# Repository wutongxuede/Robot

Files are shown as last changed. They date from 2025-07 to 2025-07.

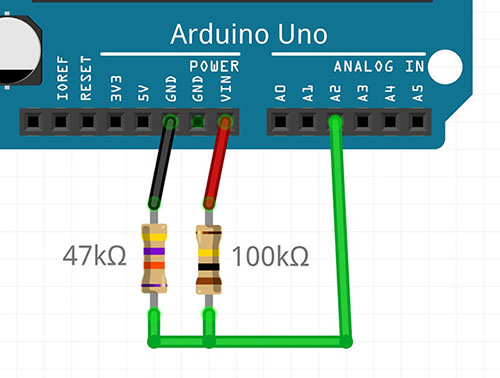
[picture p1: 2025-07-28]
Connection tutorial diagram/7.png

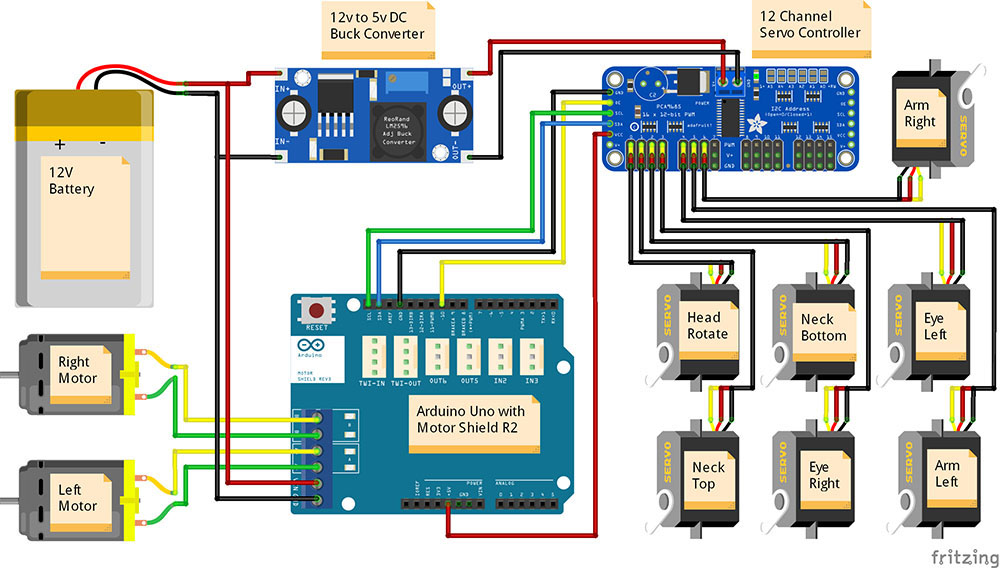
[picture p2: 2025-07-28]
Connection tutorial diagram/1.png

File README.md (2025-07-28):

# Robot
#Focus on discussions and sharing about Robot-Wall making or other DIY projects.

#The source code of the software is from the content published by Simon Bluett chillibasket on GitHub (Click to jump to GitHub for viewing: https://github.com/chillibasket/walle-replica)
## Basic introduction of the Wall-E model
1. Each eye can be independently controlled to rise and fall by a servo.

2. Each eye has space for a small camera. (We haven't done this part yet, so if you are interested, you can try it first)

3. The head can be turned left and right using a servo. (Due to the heavy weight of the head, it is recommended to use a hollow printing for the head)

4. Both joints of the neck are driven by servos, which allows the head to look up/down and raise/lower.

5. Each arm has a servo at the shoulder to move the arm up and down.

6. The arms are composed of pressure-fit joints, hands and fingers, and can be posed manually.

7. The tracks are fully 3D printed and can be driven using two 12V DC reduction motors.
**Flashing the program**
1. Please write the program to the Raspberry Pi and Arduino first, test it, and then install the circuit board into the robot.
2. The programming of the robot can be divided into two main parts; the Arduino code, and the web server on the Raspberry Pi.
Download/clone the folder wall-e from the online repository. (To add a voice recognition module, use our modified wall-e.ino main program, in the walle-replica-3.0 - modified version program folder)
Open wall-e.ino in the Arduino IDE;. In addition, the MotorController.hpp and Queue.hpp files will also automatically open on different tabs in the IDE.
Install the Adafruit_PWMServoDriver.h library
Go to Sketch -> Include Library -> Manage Libraries
Search for Adafruit PWM Servo Driver.
Install the latest version of the library
Connect the computer and the controller with a USB data cable. Make sure to select the correct board and port in the "Tools" menu.
Upload the wall-e.ino main program
**Test**
Upload the main program to the Arduino. While the Arduino is still connected to the computer, connect a 12V (3S) battery and power it on.
Open the serial port detection (the button on the upper right of the Arduino IDE), set the baud rate to 115200.
Now test the movement of Wally, send characters "w", "a", "s" or "d", which respectively represent Wally moving forward, left, backward or right. Sending 'q' can stop the movement.
Now test the head movement of Wally, send letters "j", "l", "i" or "k" to tilt the head left or right, and raise or lower the eyes. At this stage, the joints controlled by the servo motors may have a wider range than the actual due to the lack of setting for the stroke. This problem will be solved by performing the following servo calibration steps.
Servo Calibration
Download/clone the "wall-e_calibration" folder from the online repository.
Open wall-e_calibration.ino in the Arduino IDE.
Upload the program to the Arduino, open the serial monitor, and set the baud rate to 115200.
This program is used to calibrate the movement range required to move each servo motor to the corresponding position, the maximum and minimum PWM pulse widths. The standard LOW and HIGH positions of each servo are as follows.
Before installing the servo motors, it is necessary to ensure that the angles of the servo motors are correct (the range can be referred to the following figure), and then install the servo arms. Since the servo motors can only rotate 180 degrees, if they are fixed at the wrong angle, they will not be able to control the joints correctly.

After starting the program, open the serial monitor. After 2-3 seconds, a message should appear indicating that the LOW position of the first servo motor (head rotation) is ready for calibration.
Send the characters "a" and "d" to control the robot's movement forward and backward, within the range of -10 to +10. If more precise control is needed, use the characters "z" and "c" to move the robot, within the range of -1 to +1.
Once the servo is positioned at the correct position (as shown in the figure below), send the character "n" to continue the calibration steps. It will move to the HIGH position of the same servo, and then the 7 servos in the robot will repeat this process.
When all the joints have been calibrated, the program will output an array containing the calibration values to the serial monitor.
Copy this array and paste it into lines 144 to 150 of the wall-e - ino program. The array should look similar to the following:

int preset[][2] =  {{410,120},  // head rotation
                    {532,178},  // neck top
                    {120,310},  // neck bottom
                    {465,271},  // eye right
                    {278,479},  // eye left
                    {340,135},  // arm left
                    {150,360}}; // arm right
                    
**Battery level detection (optional)**
Note: When using batteries to power the robot, it is necessary to detect the battery level in real time. Over-discharge may cause battery damage, and insufficient power supply may damage the SD card of the Raspberry Pi. 
When using the battery level detection function on the Arduino, please connect the following resistors as shown in the following diagram and make the connections.

The resistor (voltage divider) reduces the 12V voltage to below 5V, allowing the Arduino to measure the voltage using its analog pins. The recommended resistor values are R1 = 100kΩ and R2 = 47kΩ.
In Arduino, remove line 54 of the main program wall-e.ino.
If you use different resistor values, please change the value of the voltage divider gain factor in line 54 of the program according to the formula: POT_DIV = R2 / (R1 + R2).
The program should now automatically check the battery level every 10 seconds, and this level will be displayed in the "Status" section of the Raspberry Pi network interface.
OLED display (optional) (Contributed by hpkevertje on GitHub) Notes for Attention

A 1.3-inch small OLED display can be integrated, and the battery level of the Wally robot can be displayed on the battery indicator panel. This function requires enabling the aforementioned battery detection circuit. The screen will be updated each time the battery level is calculated. 
This function uses the u8g2 display library in the page mode. 
On the Arduino UNO, you might receive a warning about high memory usage, but this warning can be ignored. 
To use the oLed display function on Arduino, connect the i2c oLed display (as shown in the picture) to the i2c bus of the servo motor module. 
Input image description 
Install the U8g2 library in the Arduino Library Manager:
In Sketch -> Include Library -> Manage Libraries
Search for U8gt (creator: oliver)
Install the latest version of the library
Define the OLED in the Arduino main program wall-e.ino.
If you are using another display method supported by the library, you can change the constructor on line 78 according to the documentation on the library reference page. The default is for the sh1106_128x64_name display.
Add custom servo actions (optional)
The source code comes with two animations that can be copied to replicate the scenes in the movie; 
The eye movements of robot Wally when it is activated, as well as a series of actions when robot Wally curiously looks around.

Starting from version 2.7, users can now add custom actions more easily. 
Open the "animations.ino" file, which is located in the same folder as the main Arduino program.
Each action command contains the position you want all the servos to move to, as well as the time the animation should wait before moving to the next instruction.
Actions can be added by inserting an additional case in the switch statement. Place the additional code above the default section in the empty space. For example: case 3:
// --- Title of your new motion sequence ---
//          time,head,necT,necB,eyeR,eyeL,armL,armR
queue.push({  12,  48,  40,   0,  35,  45,  60,  59});
queue.push({1500,  48,  40,  20, 100,   0,  80,  80});
// Add as many additional movements here as you need to complete the animation
// queue.push({time, head rotation, neck top, neck bottom, eye right, eye left, arm left, arm right})
break;
The time should be measured in milliseconds (for example, 3.5 seconds = 3500).
The position command for the servo needs to be an integer between 0 and 100, where 0 = LOW, 100 = HIGH, and the servo position calibrated in wall-e_calibration is the same.
If you want to disable a specific servo, you can set its value to -1.
Raspberry Pi Settings
Hardware Settings
Connect the power cable of the Raspberry Pi to the USB power output port of the 12V to 5V converter.
Connect the Arduino to the Raspberry Pi using a USB connection.
If you have a Raspberry Pi camera, connect the cable to the CSI camera connector.
For convenience in setting up and installing, you can insert the display into the HDMI port and connect a USB keyboard and mouse. Or connect and configure the Raspberry Pi from another computer via SSH.
Basic Settings
Install the Raspberry Pi to run the latest version of the Raspberry Pi OS Desktop. Installation instructions can be found on the Raspberry Pi website.
Ensure the Raspberry Pi is connected to the internet.
Open "Terminal" on the Raspberry Pi.
Clone the repository to the root directory of the Raspberry Pi:
cd ~

git clone https://github.com/chillibasket/walle-replica.git

The web interface settings can be configured by editing the "config.py" file:
Open the configuration file: nano ~/wall-replica/web_interface/config.py
On line 14, you can change the password for the web interface. The default password is "walle".
On line 15, you can set the default serial port for connecting to the Arduino. You can use the command "dmseg | grep tty" to find a list of all connected serial ports.
On lines 16 and 17, you can configure whether the Arduino and camera should automatically connect when starting the web server.
After completing the editing of the configuration, run the installation script and set all necessary libraries (it may take some time): cd ~/walle-replica

sudo chmod +x ./raspi-setup.sh

sudo ./raspi-setup.sh
Using the Web Server
If the installation is successful, when the Raspberry Pi is powered on, the web server will automatically start. This is accomplished using the Systemd service.
On the Raspberry Pi, you can view the web interface at http://localhost:5000
To view the interface from another computer on the same WiFi network, first you need to use the command hostname -I to determine the current IP address of the Raspberry Pi on the network
To access the web interface, open a browser on any computer/device in the same network and enter the IP address of the Raspberry Pi, followed by :5000. For example, 192.168.1.10:5000
To start controlling the robot, first ensure that the serial communication with Arduino has been initiated. To do this, go to the Settings tab in the web interface, select the correct serial port from the drop-down list, and then press the Reconnect button. If the configuration settings are correct, the device will automatically start.
Here are some commands for controlling the web interface: 
Stop the automatic web interface service: sudo systemd stop wall.service 
Disable startup on boot: sudo systemctl disable wall.service 
Re-enable the startup at boot time: sudo systemd enable wall.service 
Use the Blocky control (contributed by dkrey on GitHub) 
Starting from version 3.0, there is a new option in the web interface that allows robots to be controlled using graphical programming with drag-and-drop scripting languages. Just drag the operations you want to execute from the left sidebar and drop them into the editor area. For example, you can control Wally, rotate the motor, and play audio.
For commands to drive the motor, you may need to adjust the parameters from lines 25 to 28 at the bottom of the "config.py" file to ensure the correct speed and turning amount.
Using Blocky control (contributed by: dkrey on GitHub)
Starting from version 3.0, a new option has been added to the web interface, allowing robots to be controlled through graphical programming with drag-and-drop scripting languages. Just drag the operations you want to execute from the left sidebar and drop them into the editor area. For example, you can control Wally, rotate the motor, and play audio.
For commands to drive the motor, you may need to adjust the parameters from lines 25 to 28 at the bottom of the "config.py" file to ensure the correct speed and turning amount.
Adding video stream (optional)
The web server automatically supports any CSI connector connected to the Raspberry Pi and a ribbon cable camera. (Currently, USB network cameras are not supported.) 
Add new sound (optional)
By default, the Raspberry should automatically choose whether to output audio to the HDMI port or the headphone jack. However, the following command can be used to ensure that it always uses the headphone jack: amixer cset numid= 31
Make sure that all the sound files you want to use are of the *.wav format. Most music editors should be able to convert sound files to this format.
Modify the file name to have the format [group name][file name][sound duration (milliseconds)]. For example: voice_eva_1200.wav. In the web interface, audio files will be grouped by "group name" and sorted alphabetically.
Upload the sound files to the following folder on the Raspberry Pi: ~/wall -replica/web_interface/static/sounds/
When reloading the page, all the files should appear in the web interface. If the files do not appear, it may be necessary to change the permissions required to access this folder: sudo chmod -R 755 ~/wall -replica/web_interface/static/sounds

Set Raspberry Pi as a WiFi hotspot (optional)
The Raspberry Pi can be configured as a WiFi hotspot network. The computer/mobile phone/tablet controlling the robot can directly connect to this network.
To set up the WiFi hotspot, we will use the RaspAP project, which is responsible for all the configurations and tools to make the system work.
The following operations are based on the quick installation guide:
Update Raspian, kernel and firmware (and then restart): sudo apt-get update

sudo apt-get dist-upgrade

sudo reboot now

Make sure to set the correct WiFi country in the localization options of raspi-config: sudo raspi-config
Run the quick installation program: curl -sL https://install.raspap.com | bash
For the first few yes/no prompts during the installation process, enter "y" (yes) to accept all recommended settings.
The last two prompts (advertising interception and next) are not necessary, so you can enter "n" (no).
Restart the Raspberry Pi: sudo Reboot
Now the Raspberry Pi should start the WiFi hotspot network in the following way:
SSID (wifi name): raspi-webgui
Password: ChangeMe
After connecting to the WiFi network via a computer, mobile phone or tablet, enter the following address in the browser to open the Wally's network interface: http://10.3.141.1:5000
It is recommended to enter the WiFi configuration page at http://10.3.141.1 to modify the WiFi name and password. The default username is "admin" and the password is "secret".
Click on the "Hotspot" item in the left column. In the "Basic" tab, you can change the WiFi network name, and in the "Security" tab, you can change the WiFi password.
To change the admin password of the WiFi settings management interface, click the "admin" icon in the upper right corner of the interface.

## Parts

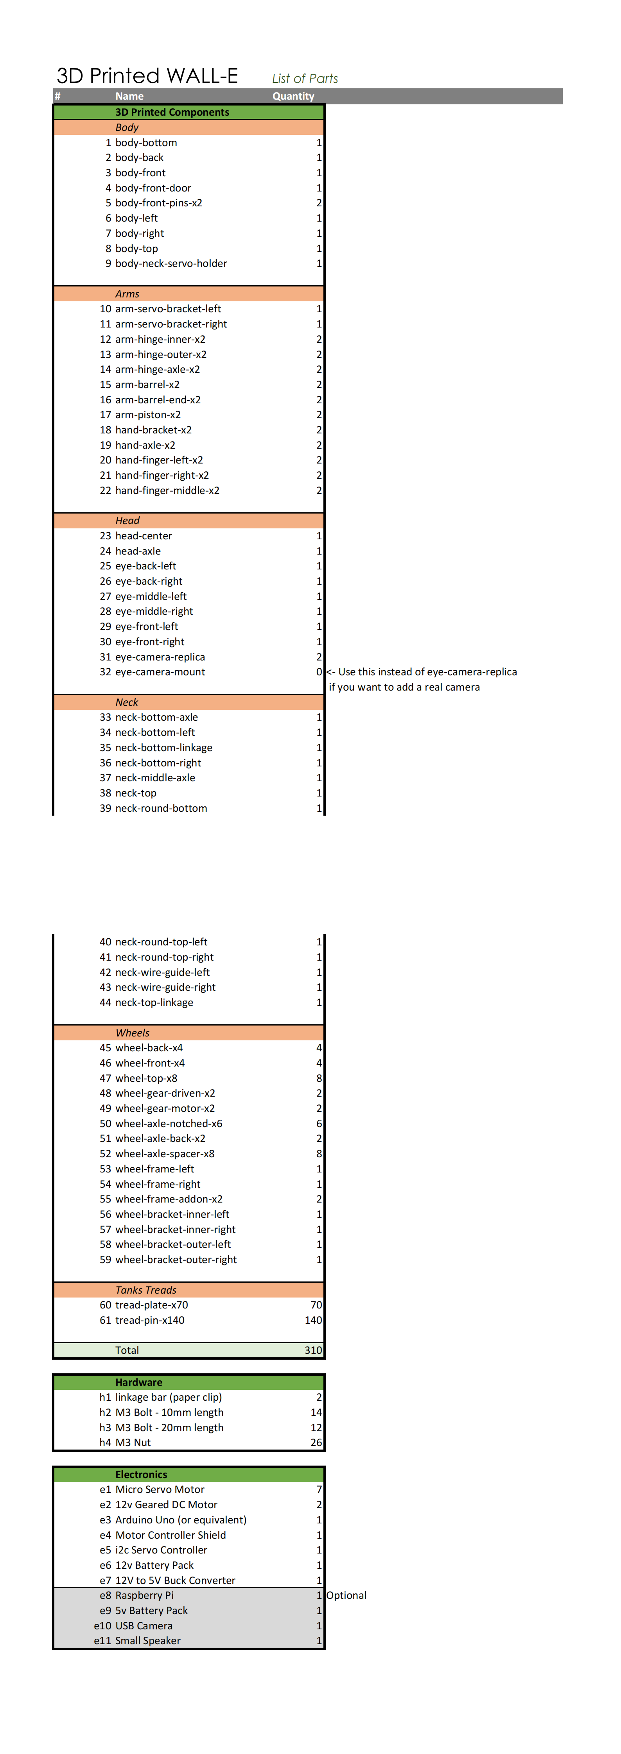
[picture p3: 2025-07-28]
Material purchase screenshot/Wall-Part quantity.png

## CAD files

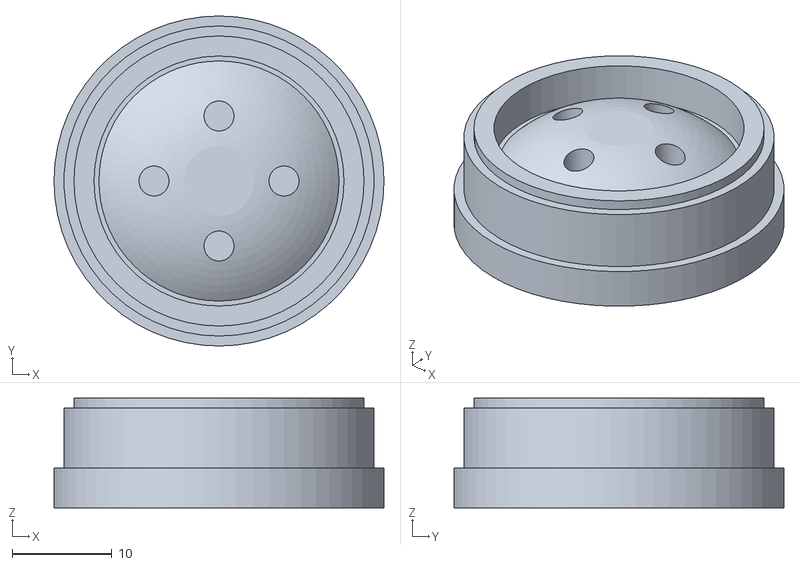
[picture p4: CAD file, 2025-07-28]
Robot-Wall 3D Printing Drawings/wheel-top-larger-x0.STL
33.0 x 33.0 x 11.0

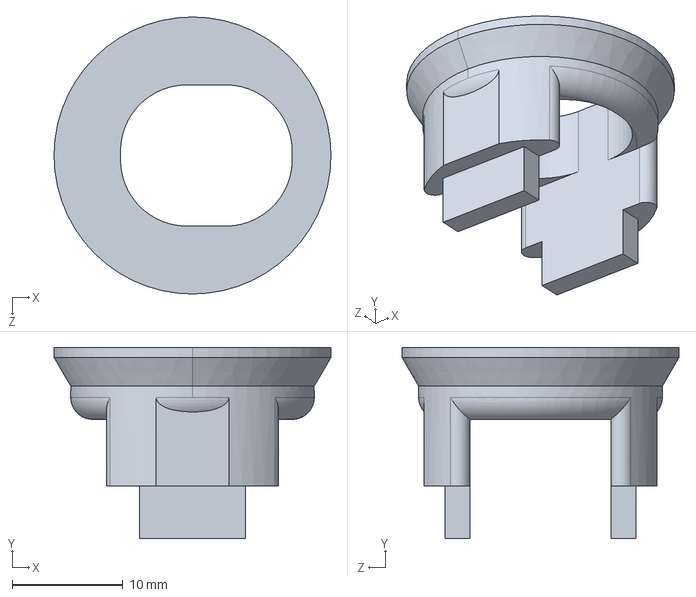
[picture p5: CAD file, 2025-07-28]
Robot-Wall drawing in STEP format, which can be used for modification/neck-round-bottom.STEP
25.0 x 17.2 x 25.0 mm

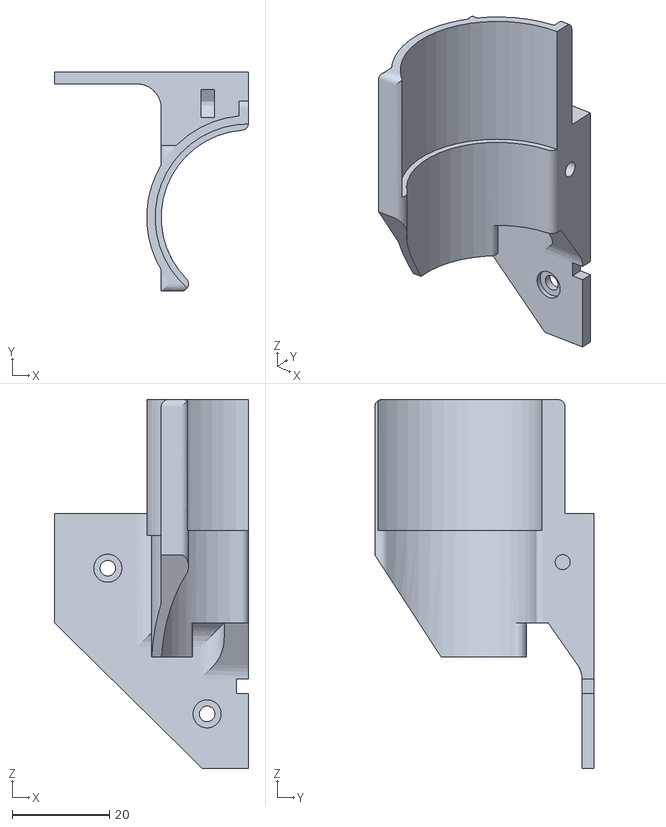
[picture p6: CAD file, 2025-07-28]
Robot-Wall 3D Printing Drawings/wheel-bracket-inner-right-3.STL
40.0 x 45.2 x 76.0

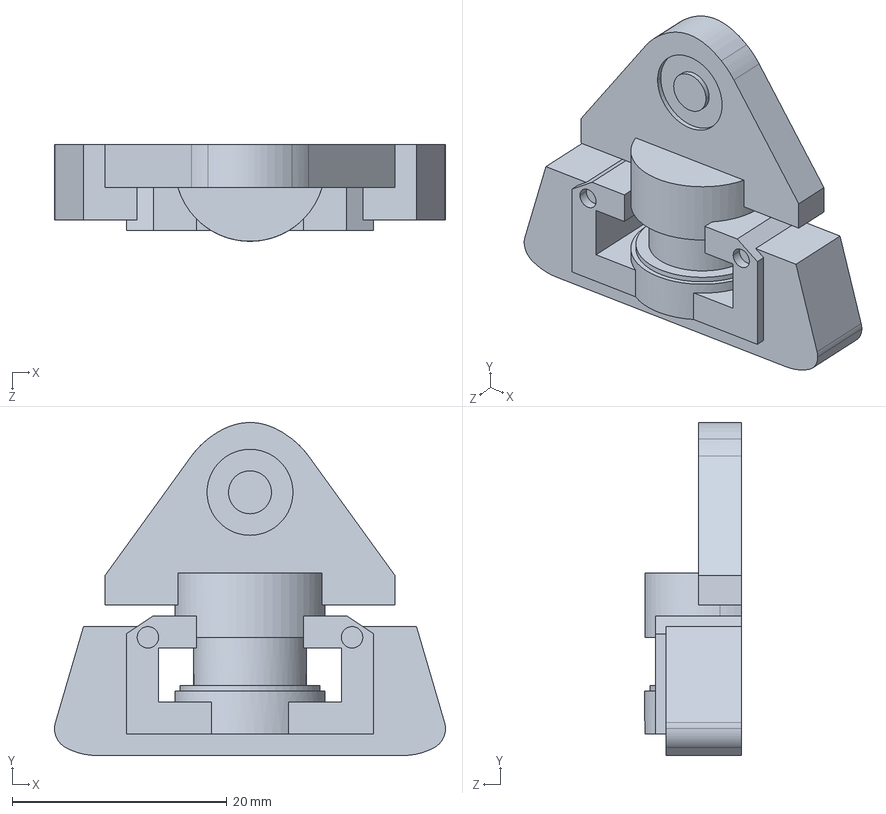
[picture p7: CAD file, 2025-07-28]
Robot-Wall drawing in STEP format, which can be used for modification/wheel-frame-addon-x2.STEP
36.4 x 31.0 x 9.00 mm

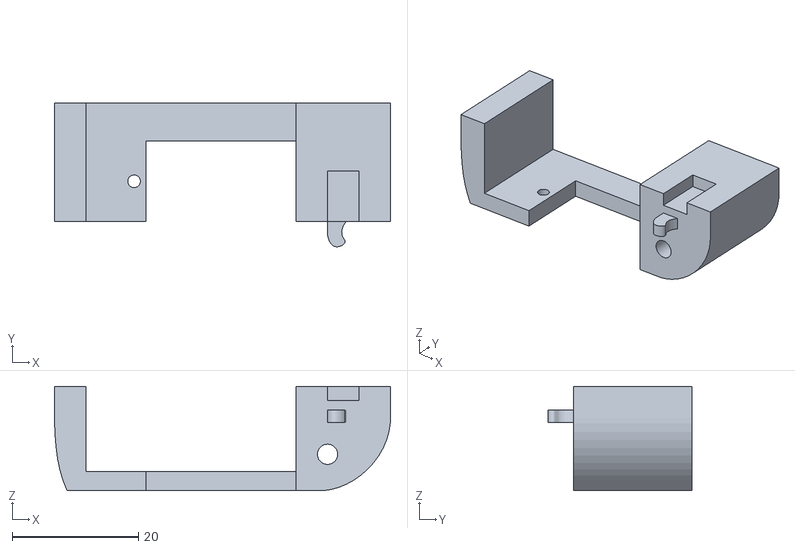
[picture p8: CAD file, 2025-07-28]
Robot-Wall 3D Printing Drawings/arm-servo-bracket-right.STL
53.2 x 22.8 x 16.5

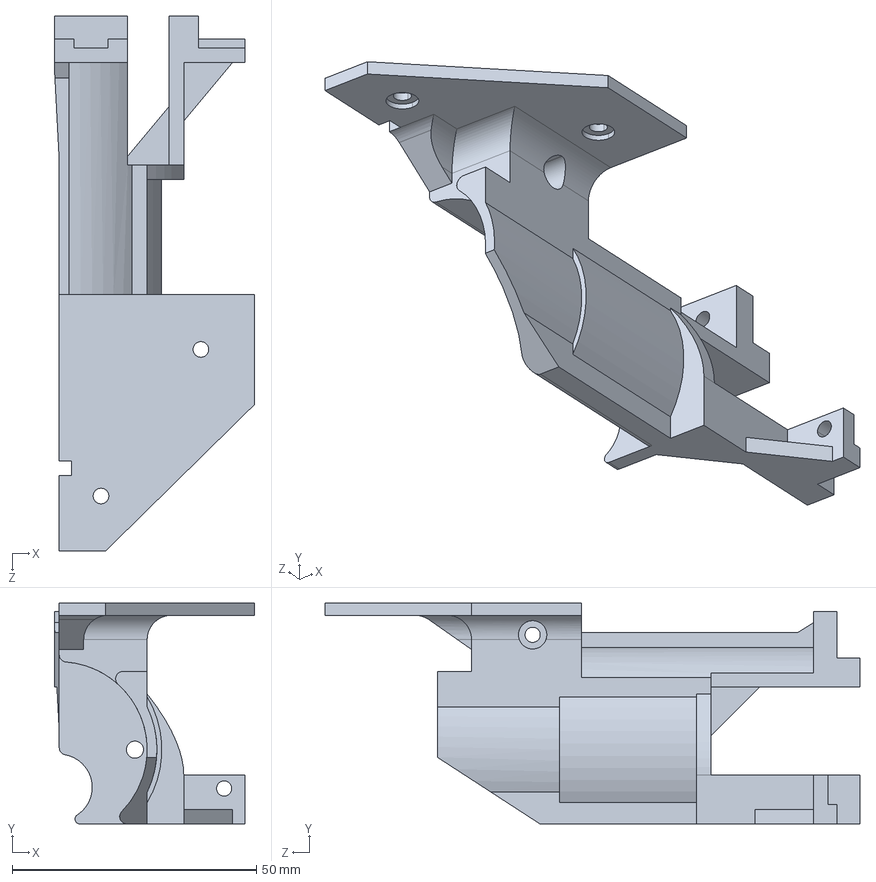
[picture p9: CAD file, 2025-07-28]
Robot-Wall drawing in STEP format, which can be used for modification/wheel-bracket-outer-left.STEP
41.0 x 45.2 x 109.5 mm

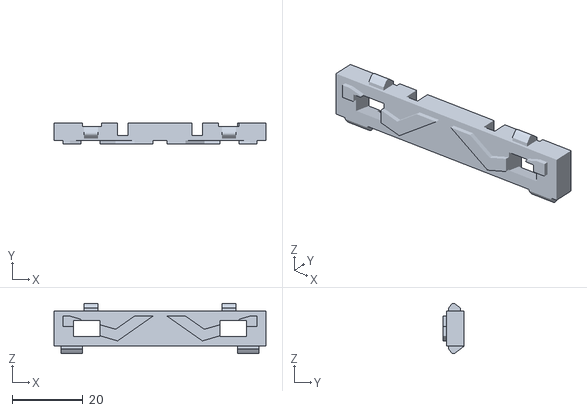
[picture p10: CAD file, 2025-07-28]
Robot-Wall 3D Printing Drawings/tread-plate-x70.STL
60.0 x 6.00 x 14.2

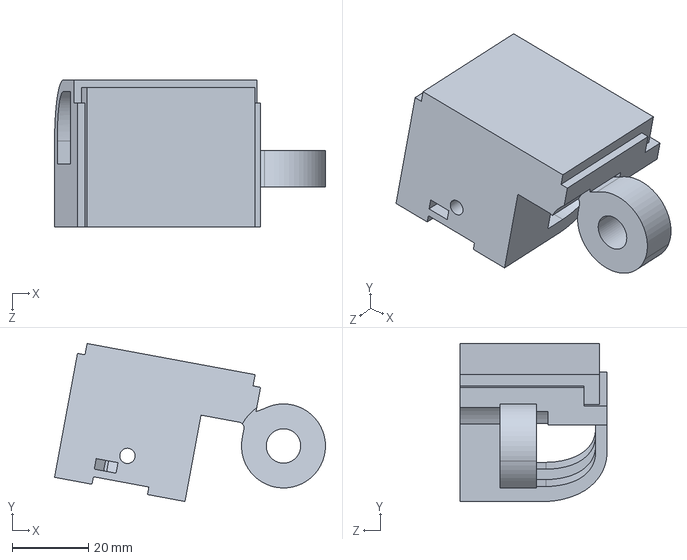
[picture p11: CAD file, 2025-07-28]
Robot-Wall drawing in STEP format, which can be used for modification/eye-back-right.STEP
70.9 x 41.4 x 38.5 mm

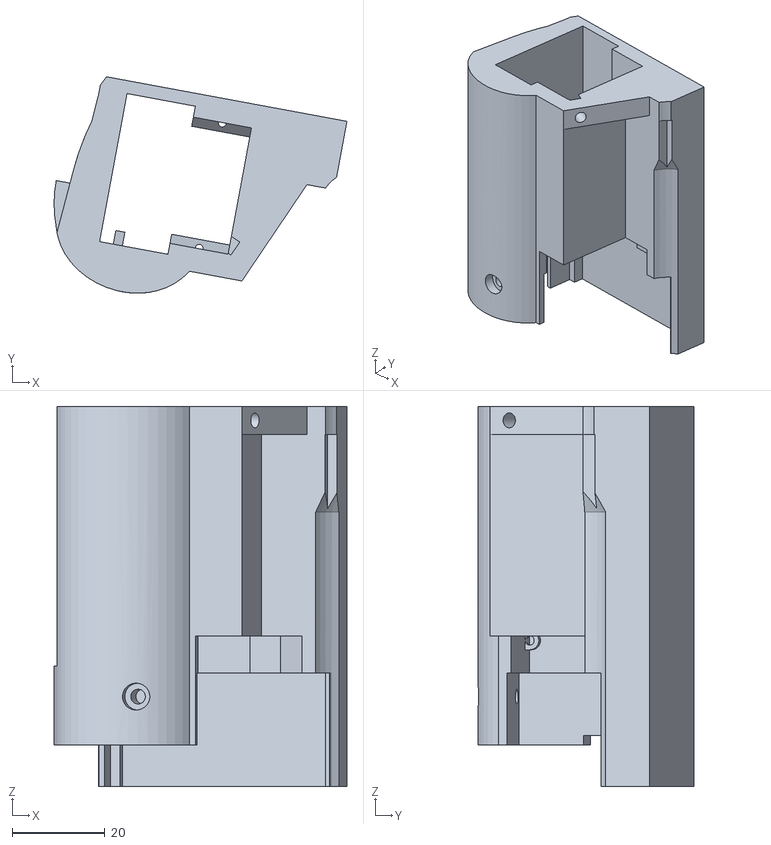
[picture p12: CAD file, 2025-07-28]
Robot-Wall 3D Printing Drawings/eye-middle-right.STL
63.2 x 46.7 x 82.0

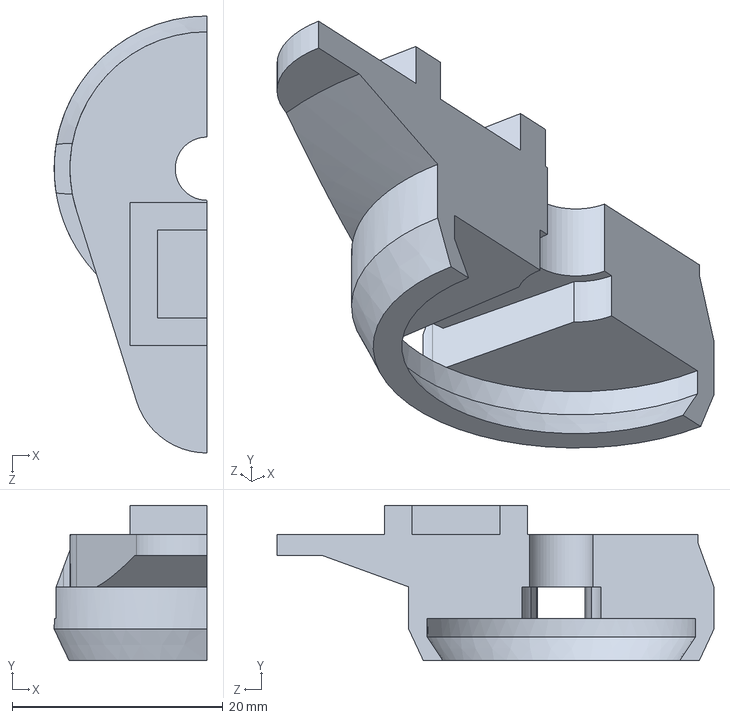
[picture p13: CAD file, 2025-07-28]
Robot-Wall drawing in STEP format, which can be used for modification/neck-round-top-left.STEP
14.5 x 14.8 x 41.5 mm

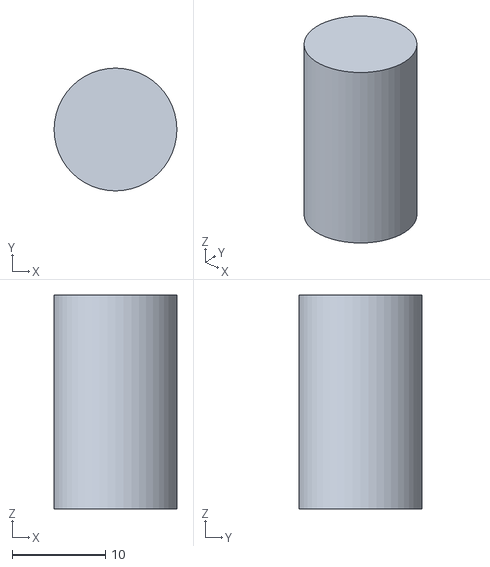
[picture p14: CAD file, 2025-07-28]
Robot-Wall 3D Printing Drawings/arm-hinge-axle-x2.STL
13.2 x 13.2 x 23.0

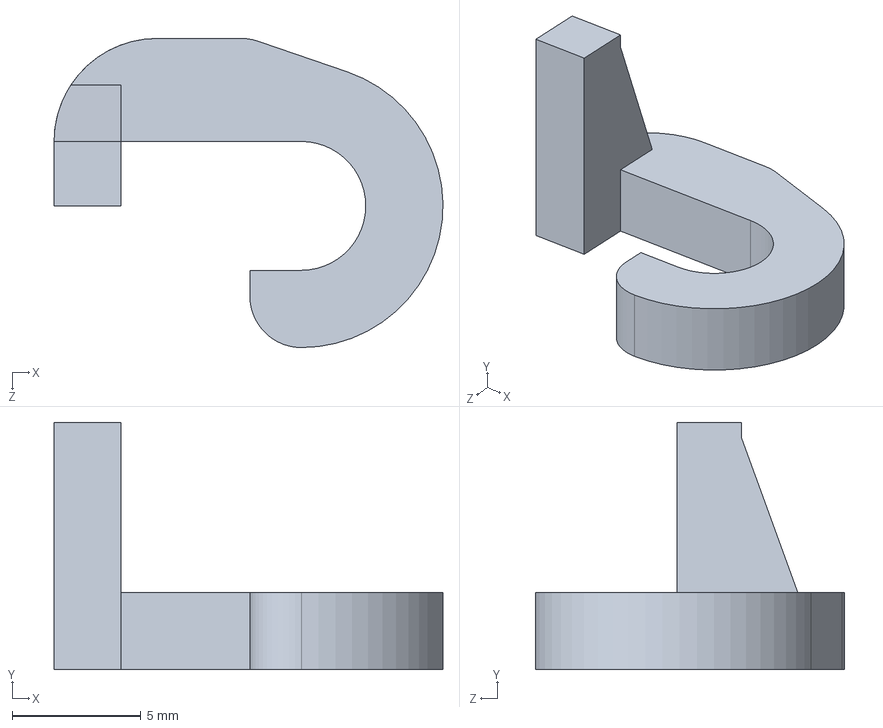
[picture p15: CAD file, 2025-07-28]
Robot-Wall drawing in STEP format, which can be used for modification/neck-wire-guide-right.STEP
15.1 x 9.60 x 12.0 mm

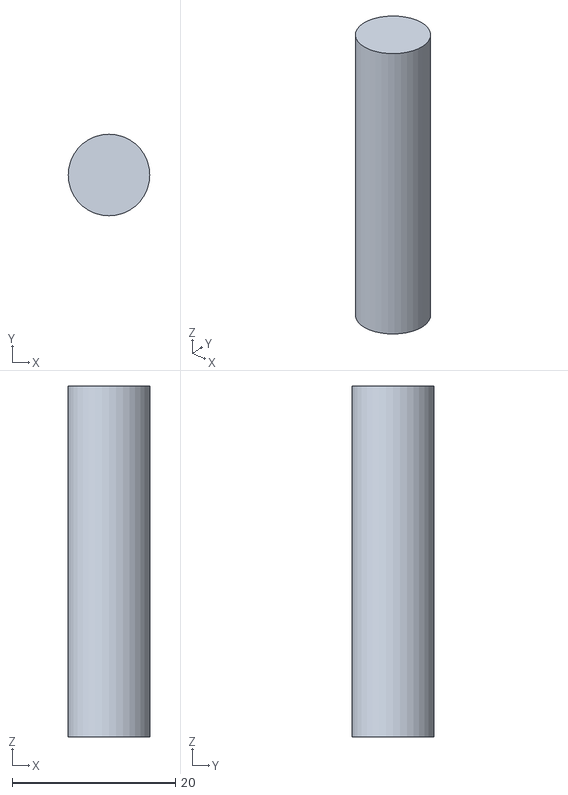
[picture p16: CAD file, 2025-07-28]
Robot-Wall 3D Printing Drawings/wheel-axle-back-x2.STL
10.0 x 10.0 x 43.0

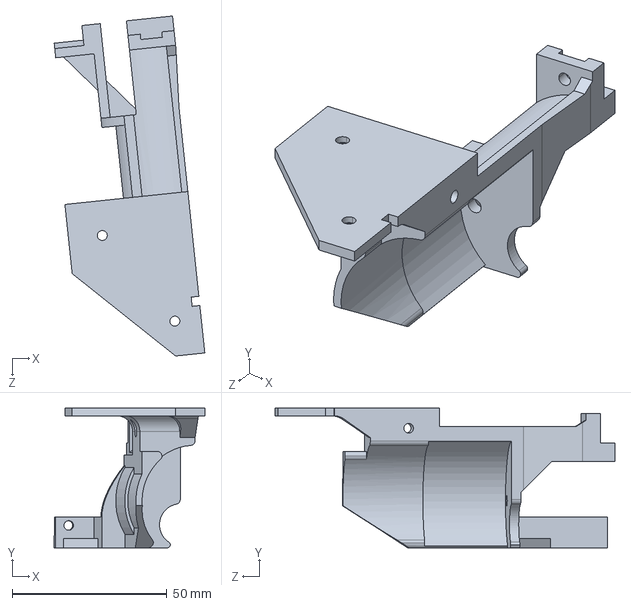
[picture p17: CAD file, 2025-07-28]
Robot-Wall drawing in STEP format, which can be used for modification/wheel-bracket-outer-right.STEP
48.7 x 45.2 x 110.0 mm

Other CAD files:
Robot-Wall 3D Printing Drawings/wheel-axle-notched-x6.STL
Robot-Wall drawing in STEP format, which can be used for modification/eye-camera-mount.STEP
Robot-Wall 3D Printing Drawings/eye-front-left.STL
Robot-Wall drawing in STEP format, which can be used for modification/body-left.STEP
Robot-Wall 3D Printing Drawings/arm-barrel-end-x2.STL
Robot-Wall 3D Printing Drawings/arm-barrel-x2.STL
Robot-Wall 3D Printing Drawings/arm-hinge-inner-x2.STL
Robot-Wall 3D Printing Drawings/arm-hinge-outer-x2.STL
Robot-Wall 3D Printing Drawings/arm-piston-x2.STL
Robot-Wall 3D Printing Drawings/arm-servo-bracket-left.STL
Robot-Wall 3D Printing Drawings/body-back.STL
Robot-Wall 3D Printing Drawings/body-bottom.STL
Robot-Wall 3D Printing Drawings/body-front-door.STL
Robot-Wall 3D Printing Drawings/body-front-pins-x2.STL
Robot-Wall 3D Printing Drawings/body-front-power.STL
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

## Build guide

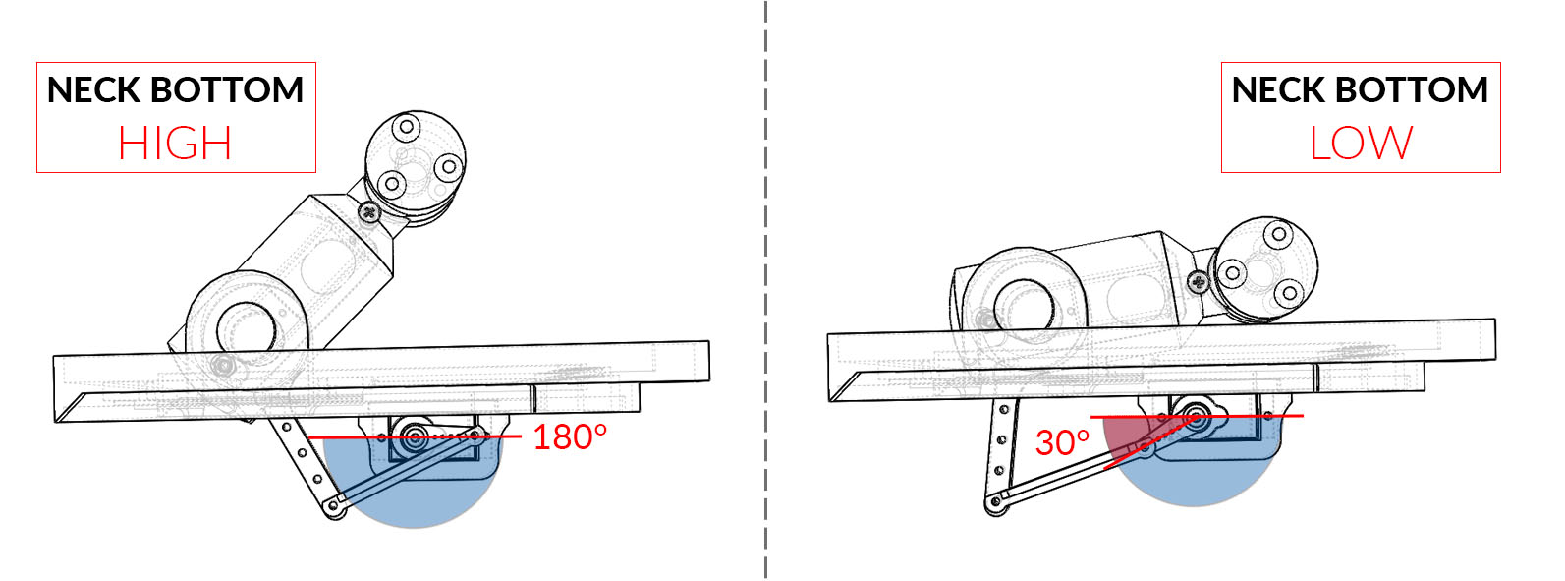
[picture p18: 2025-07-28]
Connection tutorial diagram/2.png

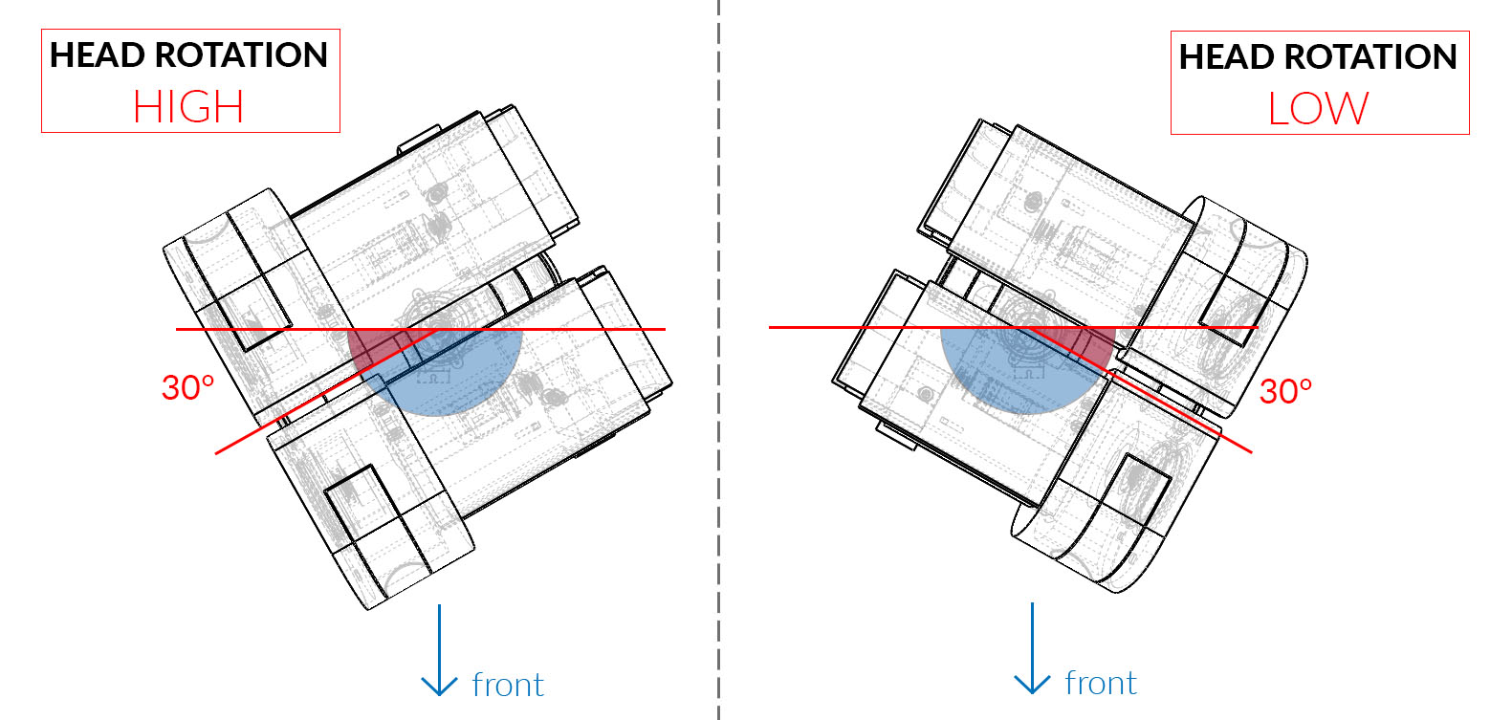
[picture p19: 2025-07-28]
Connection tutorial diagram/4.png

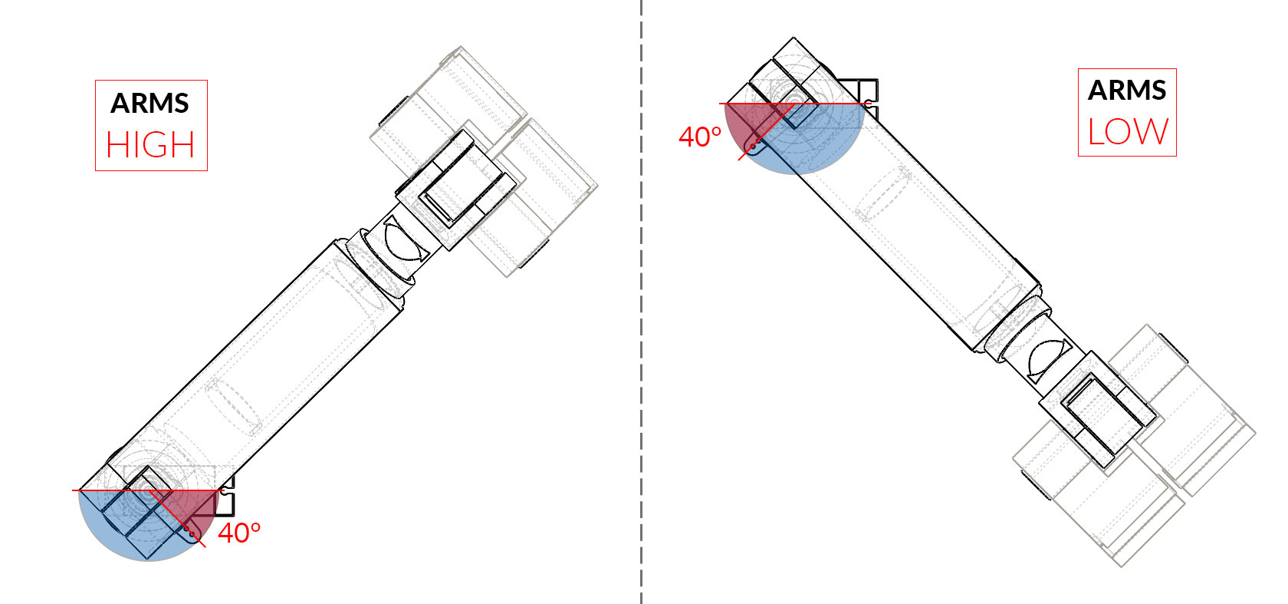
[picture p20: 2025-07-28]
Connection tutorial diagram/6.png
